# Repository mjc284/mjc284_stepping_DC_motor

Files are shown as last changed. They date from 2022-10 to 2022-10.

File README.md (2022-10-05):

# mjc284_stepping_DC_motor
Complete software and hardware build of a stepping DC motor using permanent magnets.

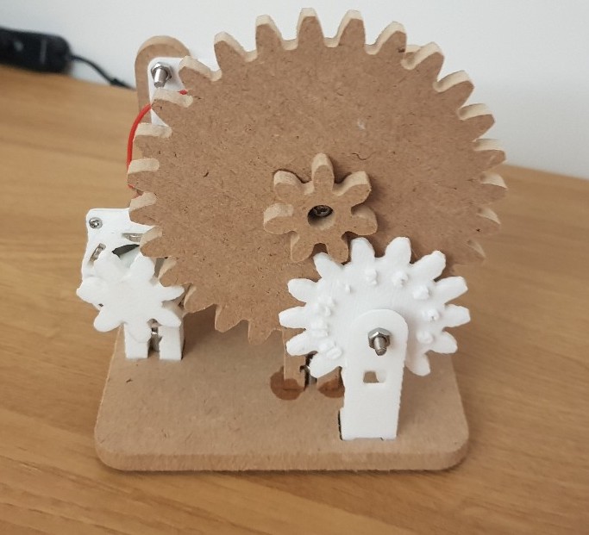
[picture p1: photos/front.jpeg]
Front


### Video demonstration:
https://www.youtube.com/watch?v=WFz_ZSToyOA

### Concept:
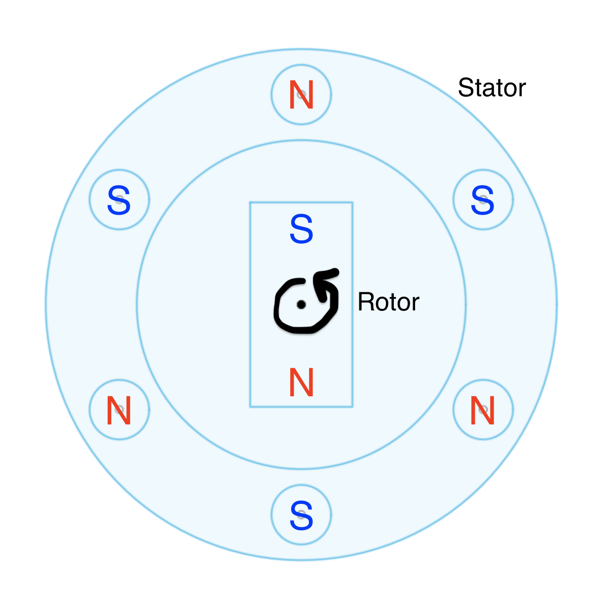
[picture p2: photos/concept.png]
Concept

The main focus of this project was to find a way to precisely control the angle of a DC motor in a similar way to stepper motors. This was achieved by attaching permenant magnets to the DC motor shaft, and creating magnetic potential 'wells' around the shaft for the rotor to fall into. In simple terms, the rotor magnet wants to be adjacent to opposite poles on the stator, giving the rotor only 3 possible states to rest on. Therefore, the motor would be driven by pulses to 'step' from one state from another, which is similar to how a stepper motor moves (although the driving operation is different). 

The output of the rotor was geared down to drive a numbered disc which represents a clock. On the electrical side, a 3-legged inverter that I designed for general purpose was used, where only two of the legs were utilized as an H-bridge. The motor 'stepping' was driven in a sequence as follows: a clockwise pulse, momentary off-state, a shorter anticlockwise pulse, and finally an off state. The anticlockwise pulse was necessary to prevent the rotor from rotating beyond the next desired state.

### Project Workflow:
- All the hardware and circuit were modelled using Fusion 360.
- Some of the parts were machined from 6mm MDF using a desktop-CNC. 
- Some of the parts were 3D-printed with postprocessing from Ultimaker-Cura.
- PCB was manufactured from the Fusion 360 gerber file by Chinese PCB services.
- Arduino-pro mini was programmed and used to drive the circuit.

### Possible Improvements:
- A better way to machine the parts with better accuracy would prevent the rotor from skipping steps occasionally.
- The rotor oscillates when it falls into the magnetic potential well. Perhaps this may be modelled as a harmonic oscillator and the stator dampened critically to prevent such oscillations.

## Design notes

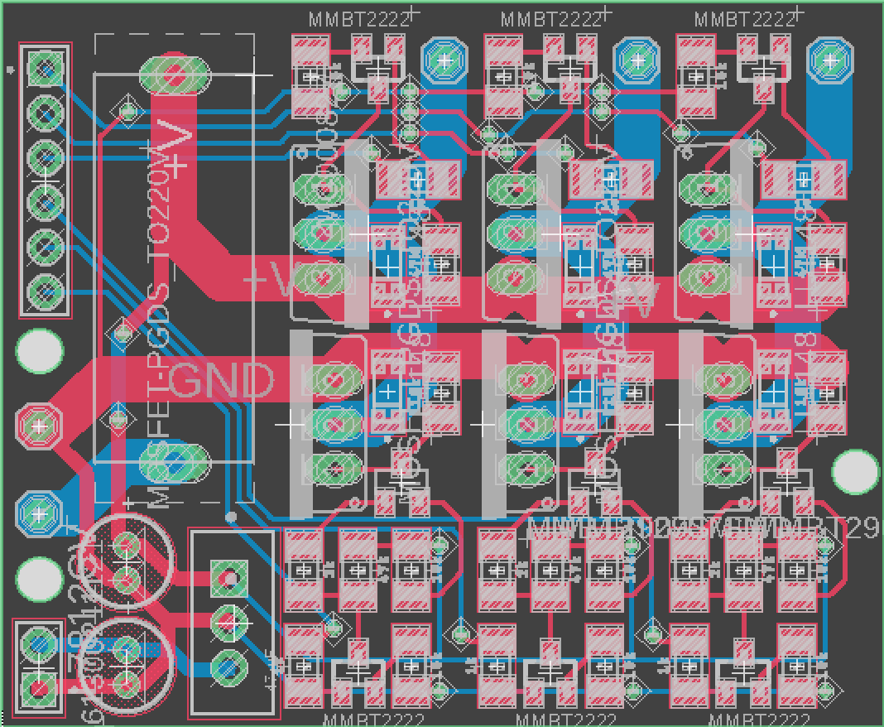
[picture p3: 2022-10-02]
project_files/hardware/circuit/circuit_board.png

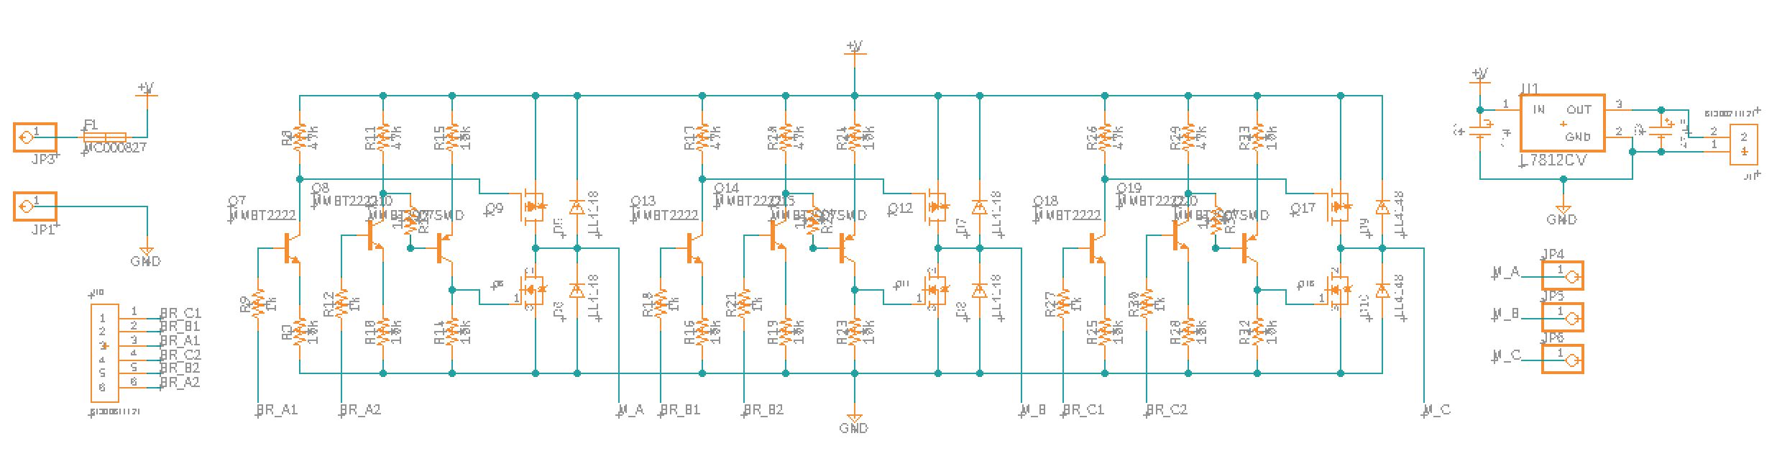
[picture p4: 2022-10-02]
project_files/hardware/circuit/circuit_schematic.png

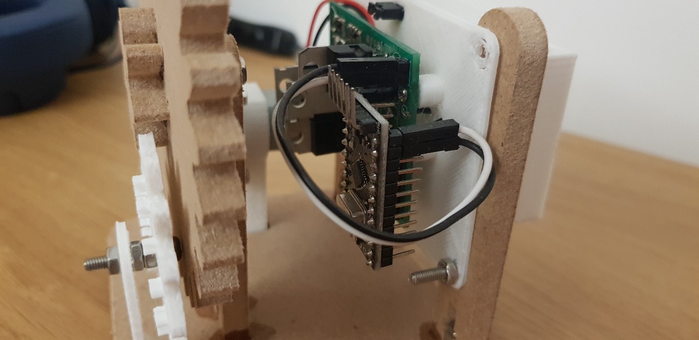
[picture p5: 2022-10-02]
photos/right.jpeg

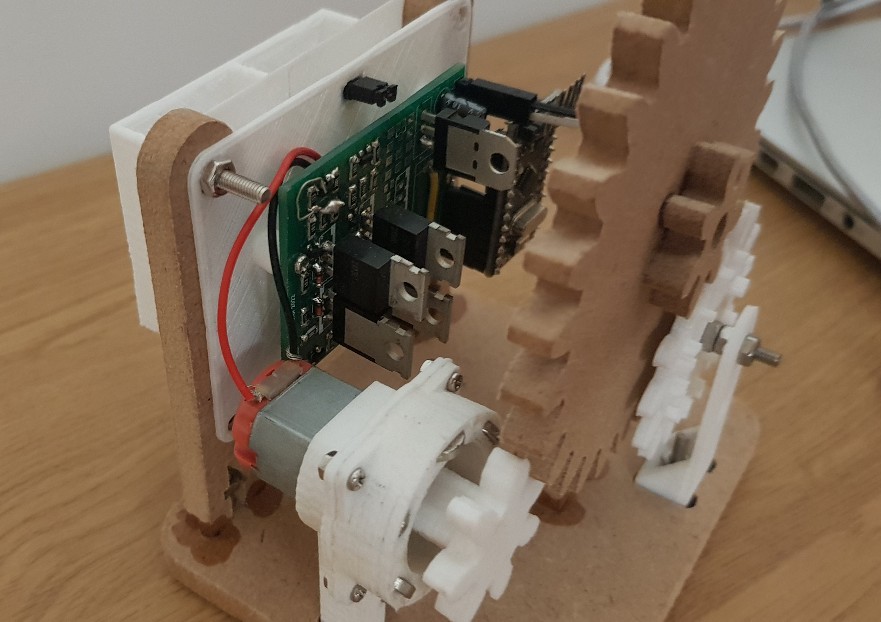
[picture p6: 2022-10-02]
photos/left.jpeg

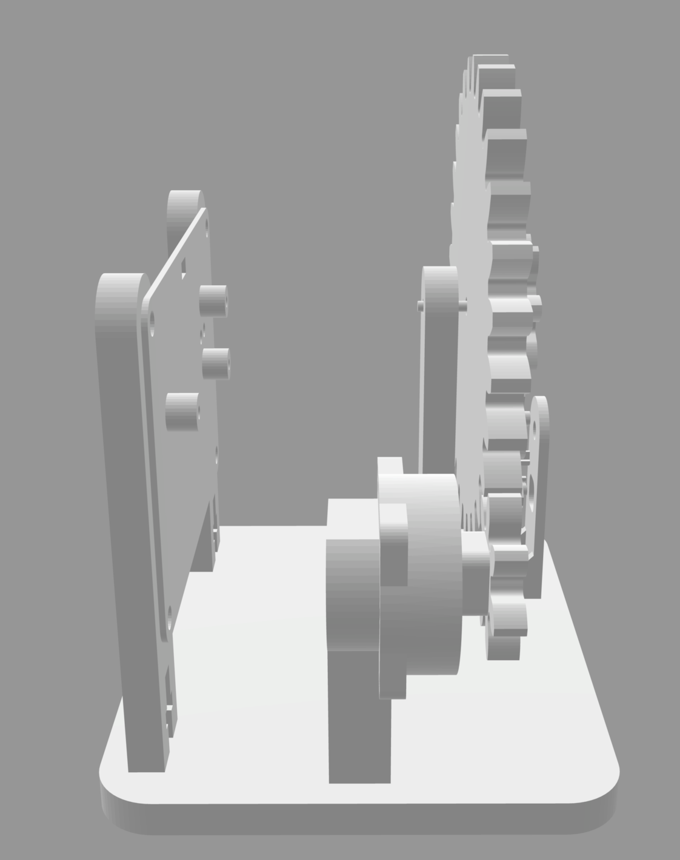
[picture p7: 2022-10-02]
photos/model_left.png

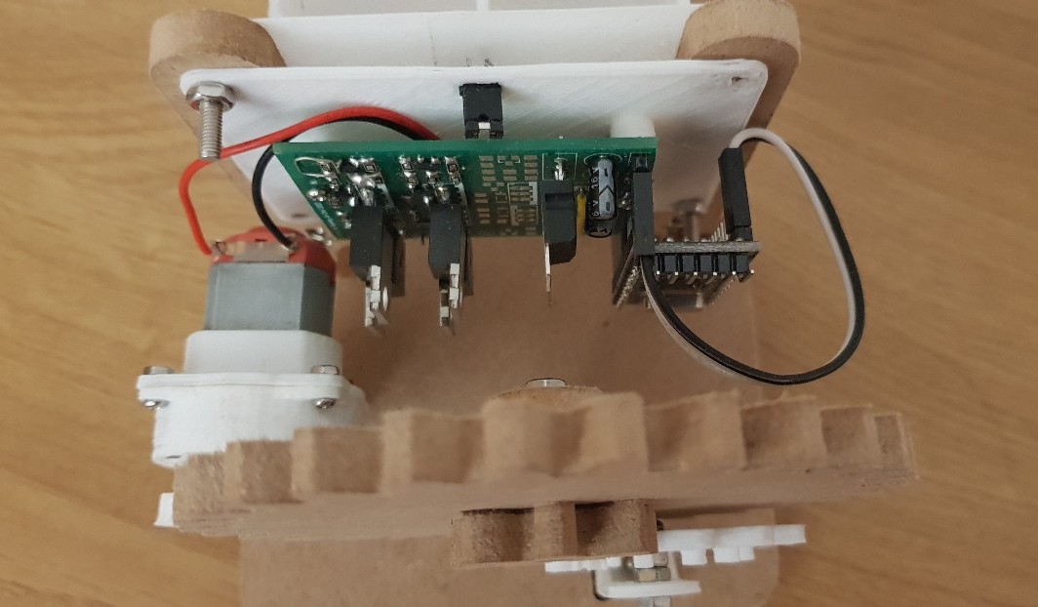
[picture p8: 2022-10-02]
photos/top.jpeg

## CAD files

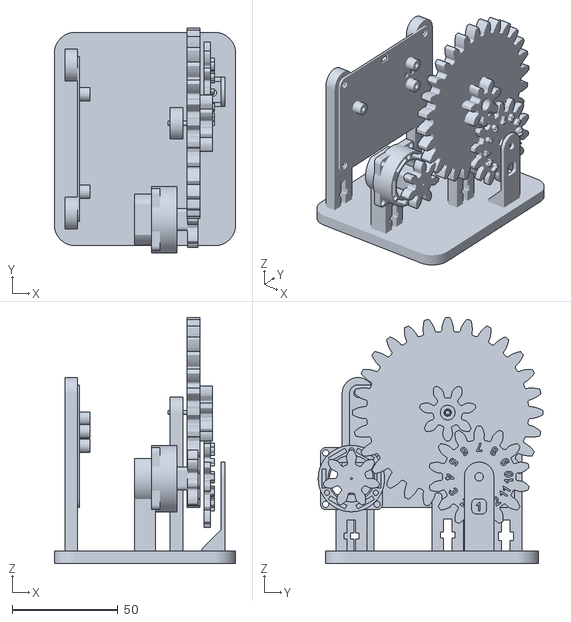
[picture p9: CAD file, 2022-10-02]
project_files/hardware/components/assembly v17.stl
85.8 x 106.3 x 116.4

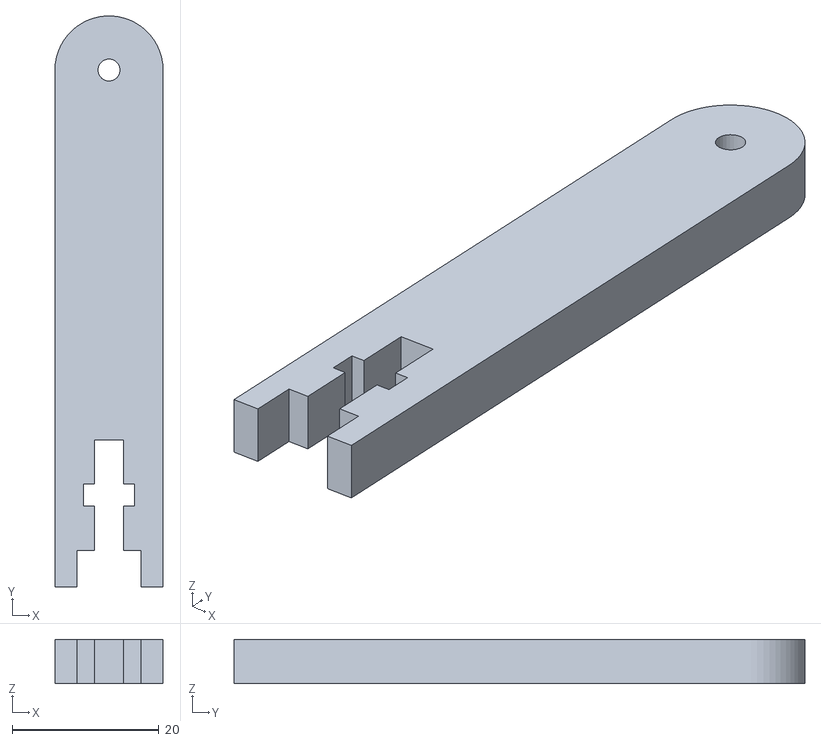
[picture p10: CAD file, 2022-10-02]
project_files/hardware/components/gear_mount v3.stl
14.7 x 77.7 x 6.00

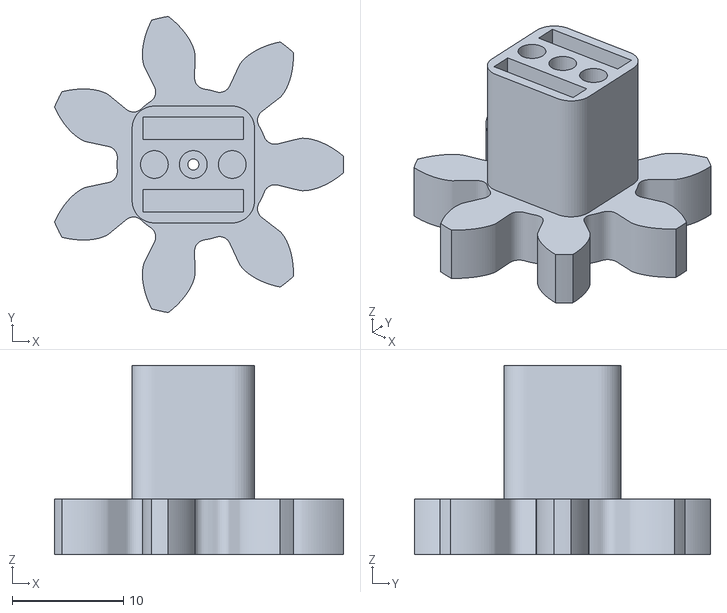
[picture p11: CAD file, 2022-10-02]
project_files/hardware/components/choistepper_gear v2.stl
26.0 x 26.6 x 17.0

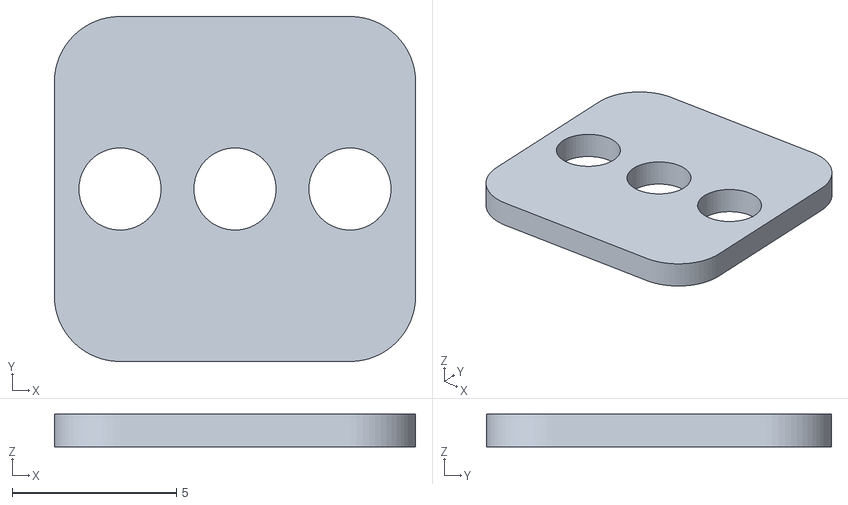
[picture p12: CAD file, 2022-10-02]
project_files/hardware/components/choistepper_gear_cap v2.stl
11.0 x 10.5 x 1.00

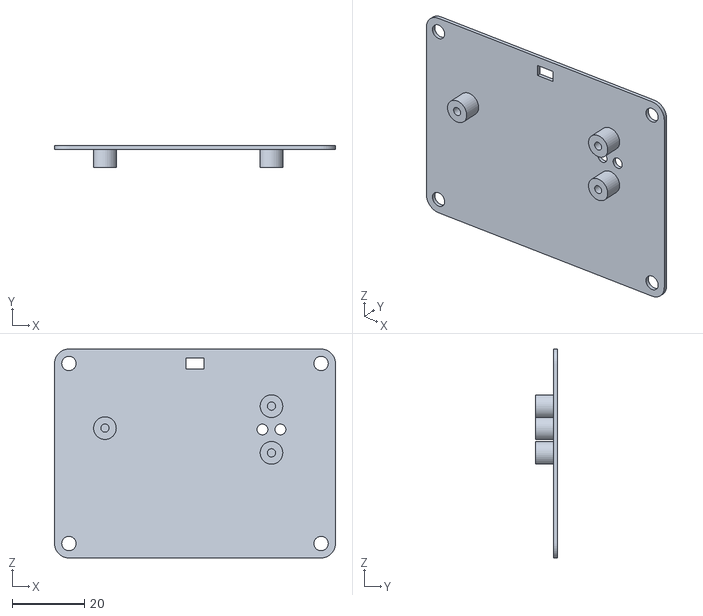
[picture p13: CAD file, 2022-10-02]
project_files/hardware/components/circuit_mount_plane v3.stl
78.0 x 6.00 x 58.0

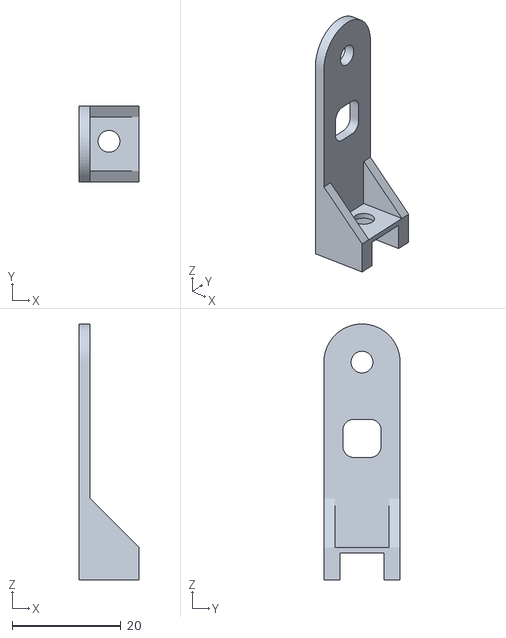
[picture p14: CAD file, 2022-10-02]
project_files/hardware/components/final_gear_mount v11.stl
11.0 x 14.0 x 47.0

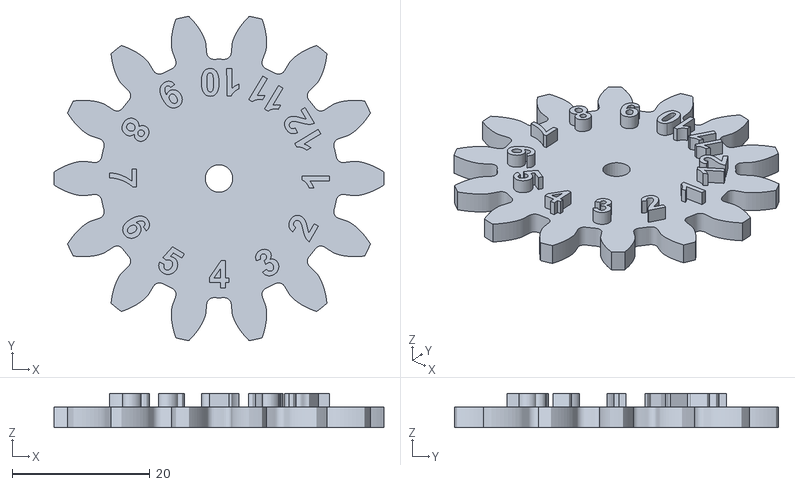
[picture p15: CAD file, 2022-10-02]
project_files/hardware/components/final_gear v11.stl
48.0 x 47.2 x 5.00

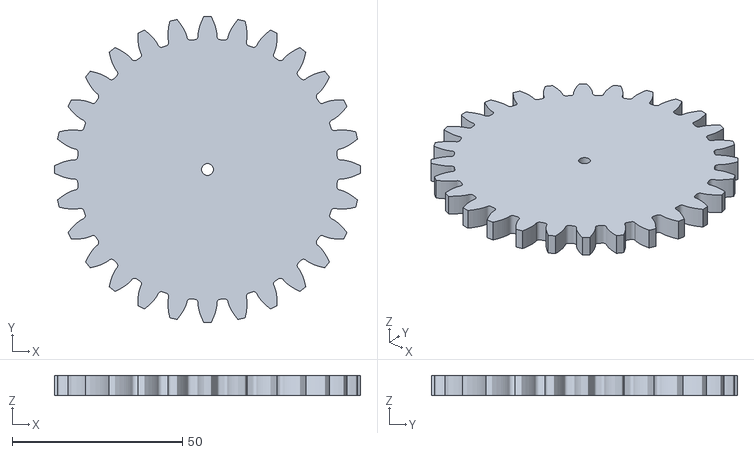
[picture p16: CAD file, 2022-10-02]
project_files/hardware/components/big_gear v6.stl
90.0 x 90.0 x 6.00

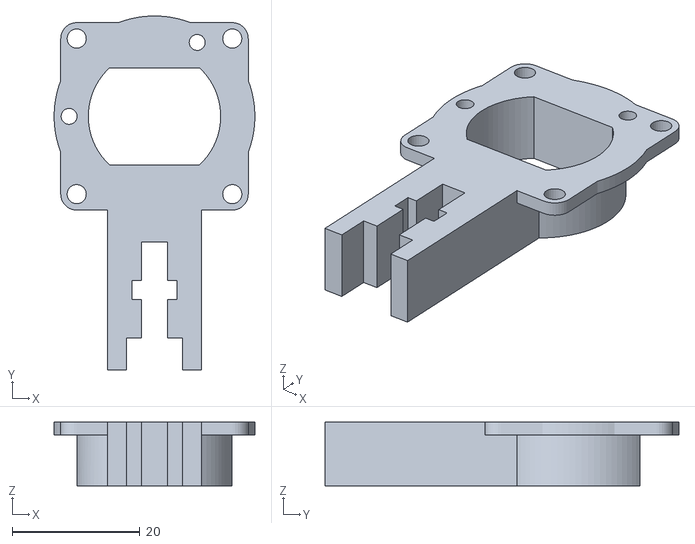
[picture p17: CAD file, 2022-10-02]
project_files/hardware/components/choistepper_mount v5.stl
31.4 x 55.4 x 10.0

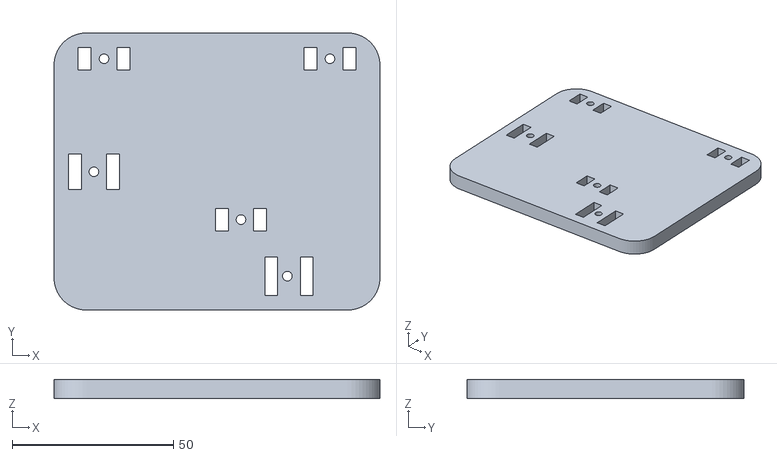
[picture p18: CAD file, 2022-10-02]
project_files/hardware/components/base v3.stl
101.0 x 85.8 x 6.00

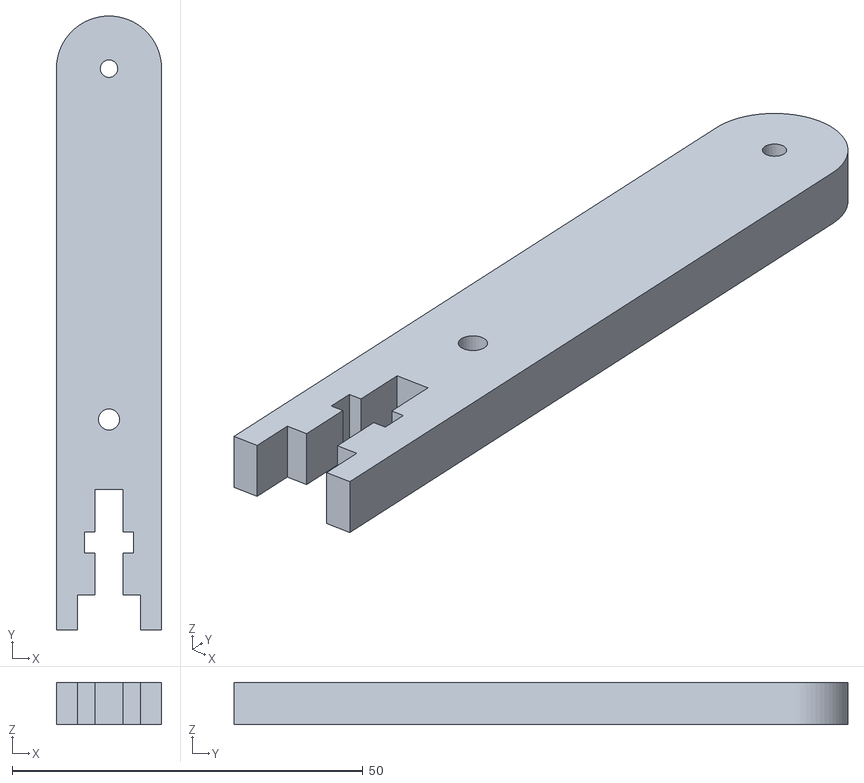
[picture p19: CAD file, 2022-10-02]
project_files/hardware/components/circuit_mount v3.stl
15.0 x 87.5 x 6.00

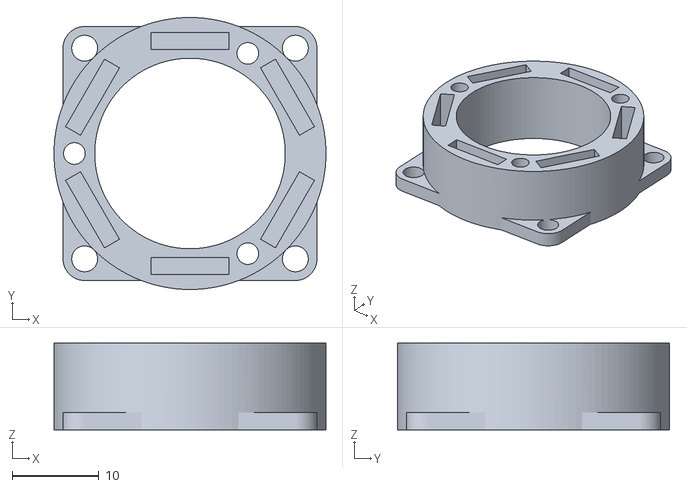
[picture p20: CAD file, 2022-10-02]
project_files/hardware/components/choistepper v4.stl
31.4 x 31.4 x 10.0

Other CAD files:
project_files/hardware/components/base v3.f3d
project_files/hardware/components/big_gear v6.f3d
project_files/hardware/components/choistepper v4.f3d
project_files/hardware/components/choistepper_gear v2.f3d
project_files/hardware/components/choistepper_gear_cap v2.f3d
project_files/hardware/components/choistepper_mount v5.f3d
project_files/hardware/components/circuit_mount v3.f3d
project_files/hardware/components/circuit_mount_plane v3.f3d
project_files/hardware/components/final_gear v11.f3d
project_files/hardware/components/final_gear_mount v11.f3d
project_files/hardware/components/gear_mount v3.f3d

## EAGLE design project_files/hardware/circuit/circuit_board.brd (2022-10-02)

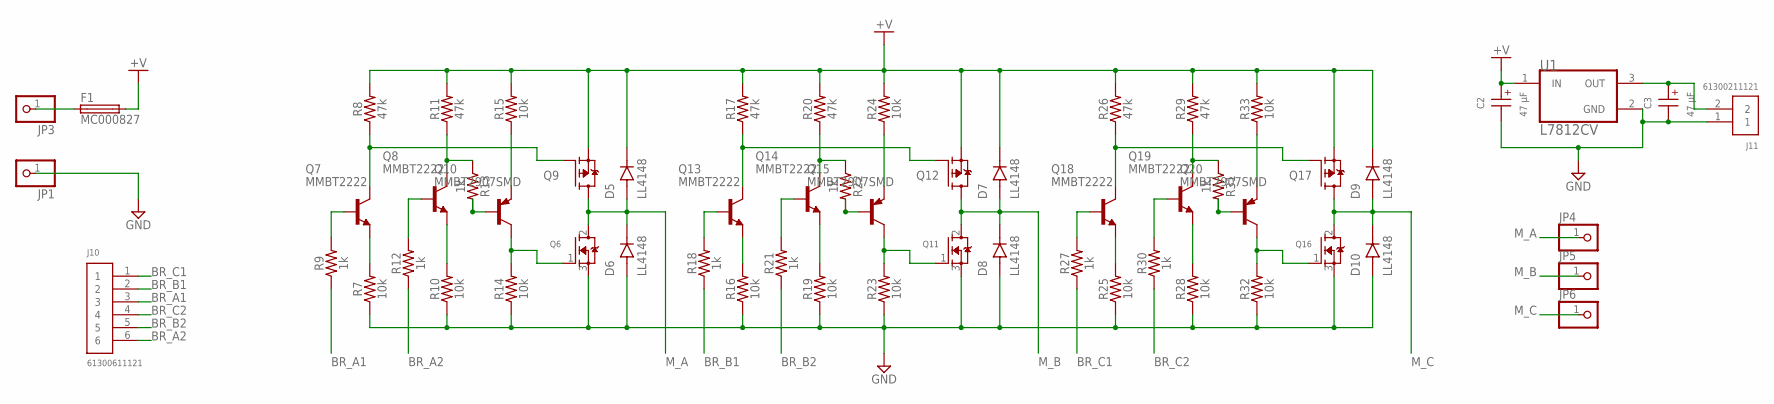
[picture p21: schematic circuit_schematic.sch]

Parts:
C2, C3: 47 µF; WCAP-ATET_5X11(DXL)
D5, D6, D7, D8, D9, D10: LL4148; DIO_LL4148
F1: MC000827
J10: 61300611121
J11: 61300211121
JP1, JP3, JP4, JP5, JP6: PINHD-1X1; 1X01
Q6, Q11, Q16: MOSFET-NGDS_TO220V; TO220V
Q7, Q8, Q13, Q14, Q18, Q19: MMBT2222; SOT23-BEC
Q9, Q12, Q17: MOSFET-PGDS_TO220V; TO220V
Q10, Q15, Q20: MMBT2907SMD; SOT23-BEC
R7, R10, R14, R15, R16, R19, R23, R24, R25, R28, R32, R33: 10k; 1206
R8, R11, R17, R20, R26, R29: 47k; 1206
R9, R12, R13, R18, R21, R22, R27, R30, R31: 1k; 1206
U1: L7812CV; TO-220-3

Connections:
+V: C2.1 (+), D5.C, D7.C, D9.C, F1.P$2 (2), Q9.3 (S), Q12.3 (S), Q17.3 (S), R8.2, R11.2, R15.2, R17.2, R20.2, R24.2, R26.2, R29.2, R33.2, U1.1 (IN)
BR_A1: J10.3, R9.1
BR_A2: J10.6, R12.1
BR_B1: J10.2, R18.1
BR_B2: J10.5, R21.1
BR_C1: J10.1, R27.1
BR_C2: J10.4, R30.1
GND: C2.2 (-), C3.2 (-), D6.A, D8.A, D10.A, J11.1, JP1.1, Q6.3 (S), Q11.3 (S), Q16.3 (S), R7.1, R10.1, R14.1, R16.1, R19.1, R23.1, R25.1, R28.1, R32.1, U1.2 (GND)
M_A: D5.A, D6.C, JP4.1, Q6.2 (D), Q9.2 (D)
M_B: D7.A, D8.C, JP5.1, Q11.2 (D), Q12.2 (D)
M_C: D9.A, D10.C, JP6.1, Q16.2 (D), Q17.2 (D)
unnamed: Q8.C, R11.1, R13.1
unnamed: Q8.B, R12.2
unnamed: Q8.E, R10.2
unnamed: Q6.1 (G), Q10.C, R14.2
unnamed: Q10.E, R15.1
unnamed: Q7.B, R9.2
unnamed: Q7.C, Q9.1 (G), R8.1
unnamed: Q7.E, R7.2
unnamed: Q10.B, R13.2
unnamed: F1.P$1 (1), JP3.1
unnamed: Q14.C, R20.1, R22.1
unnamed: Q14.B, R21.2
unnamed: Q14.E, R19.2
unnamed: Q11.1 (G), Q15.C, R23.2
unnamed: Q15.E, R24.1
unnamed: Q13.B, R18.2
unnamed: Q12.1 (G), Q13.C, R17.1
unnamed: Q13.E, R16.2
unnamed: C3.1 (+), J11.2, U1.3 (OUT)
unnamed: Q15.B, R22.2
unnamed: Q19.C, R29.1, R31.1
unnamed: Q19.B, R30.2
unnamed: Q19.E, R28.2
unnamed: Q16.1 (G), Q20.C, R32.2
unnamed: Q20.E, R33.1
unnamed: Q18.B, R27.2
unnamed: Q17.1 (G), Q18.C, R26.1
unnamed: Q18.E, R25.2
unnamed: Q20.B, R31.2

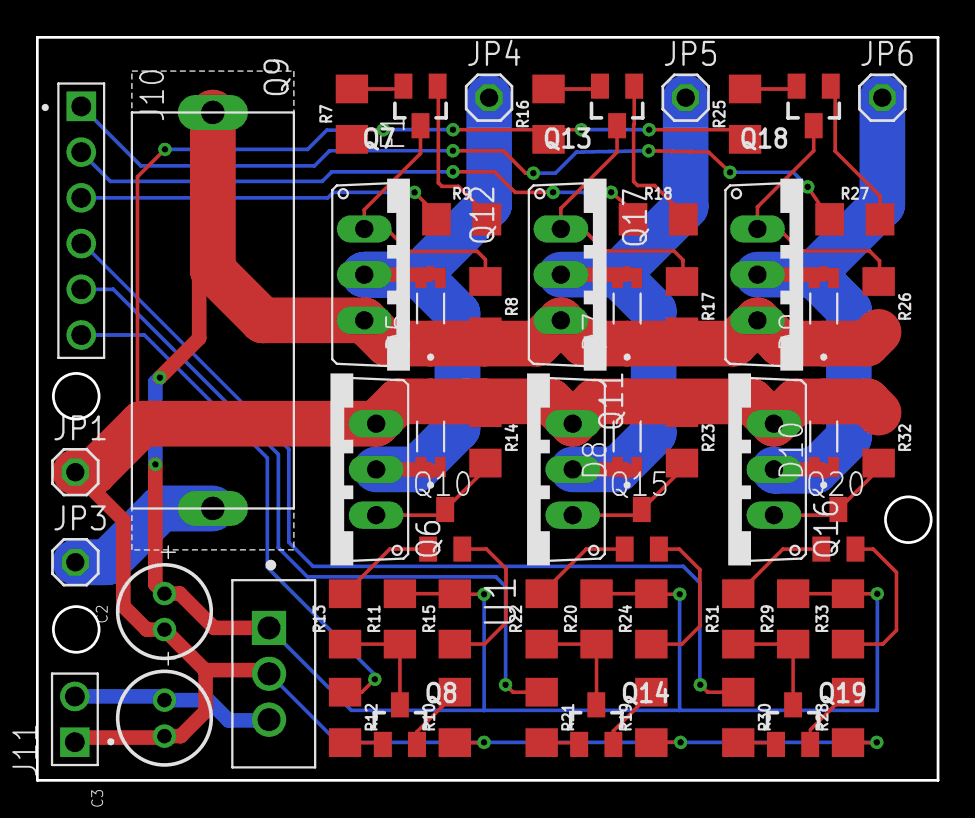
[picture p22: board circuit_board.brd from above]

Board: 2 copper layers, 50.0 x 41.3 mm, 59 parts (0 on the bottom side), 40 nets.

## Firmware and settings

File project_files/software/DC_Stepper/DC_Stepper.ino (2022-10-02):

int motor_RU = 9;
int motor_LU = 8;
int motor_RD = 6;
int motor_LD = 5;

int on_interval = 60;
int off_interval = 20;
int rev_interval = 40;

void drive(int mode)
{
  if(mode == 0)
  {
    digitalWrite(motor_RU, LOW);
    digitalWrite(motor_LU, LOW);
    digitalWrite(motor_RD, LOW);
    digitalWrite(motor_LD, LOW);
  }
  else if(mode == 1)
  {
    digitalWrite(motor_RU, LOW);
    digitalWrite(motor_LU, HIGH);
    digitalWrite(motor_RD, HIGH);
    digitalWrite(motor_LD, LOW);
  }
  else if(mode == -1)
  {
    digitalWrite(motor_RU, HIGH);
    digitalWrite(motor_LU, LOW);
    digitalWrite(motor_RD, LOW);
    digitalWrite(motor_LD, HIGH);
  }
}

void stepping(bool clockwise, int on_interval, int off_interval)
{
  if(clockwise == 1)
  {
    drive(1);
    delay(on_interval);
    drive(0);
    delay(off_interval);
    drive(-1);
    delay(rev_interval);
    drive(0);
    delay(off_interval);
  }
  else
  {
    drive(-1);
    delay(on_interval);
    drive(0);
    delay(off_interval);
    drive(1);
    delay(rev_interval);
    drive(0);
    delay(off_interval);
  }
}

void setup() {
  pinMode(motor_RU, OUTPUT);
  pinMode(motor_LU, OUTPUT);
  pinMode(motor_RD, OUTPUT);
  pinMode(motor_LD, OUTPUT);
  drive(0);
}

void loop() {
  stepping(1, on_interval, off_interval);
  delay(1000);
}

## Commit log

2022-10-02 Initiated repository.
    [assembly v17.stl, base v3.f3d, base v3.stl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]
2022-10-02 Changed src name
    [assembly v17.stl, base v3.f3d, base v3.stl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]

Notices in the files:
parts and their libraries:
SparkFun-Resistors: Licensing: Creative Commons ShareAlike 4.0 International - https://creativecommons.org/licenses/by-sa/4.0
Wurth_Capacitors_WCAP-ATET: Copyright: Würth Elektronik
